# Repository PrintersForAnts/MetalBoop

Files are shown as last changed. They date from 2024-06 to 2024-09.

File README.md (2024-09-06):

# MetalBoop

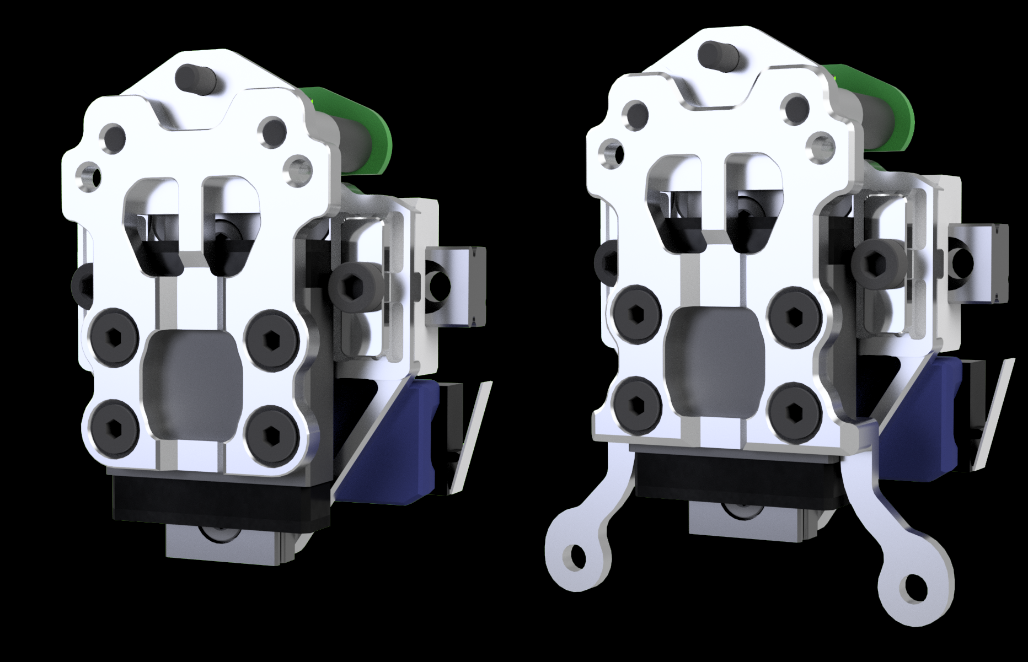
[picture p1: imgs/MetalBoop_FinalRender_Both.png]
MetalBoopRender
 

**Note: MetalBoop has been released as beta RC2 - second beta version on 6th of August 2024. Several bugs were fixed compared to RC1, but if you have no issues with RC1, there is no reason to upgrade. MetalBoop is an open source project - CAD files are available for the public [here](./CAD).**

---

### Index
1. [Introduction](#1-introduction)
2. [Features](#2-features)
3. [Compatibility](#3-compatibility)
4. [BOM](#4-bom)
5. [Assembly](#5-assembly)
6. [FAQ](#6-faq)
7. [Beta issues/changelog](#7-beta-issueschangelog)
8. [Contact](#8-contact)
9. [Credits](#9-credits)

---

## 1. Introduction

  A smaller metal version of plastic [Boop](https://github.com/PrintersForAnts/Boop).

  MetalBoop shares many of the same features as [Boop](https://github.com/PrintersForAnts/Boop) and [Tap](https://github.com/VoronDesign/Voron-Tap/) such as:
  * Microstep level accuracy.
  * Durability due to optical switch.
  * Simplicity - no dock and undock macros to fiddle with.
  * Zero probe distance.
  * Max chamber temperature: 100 C (when using OPB666N).

> [!NOTE]
> Input shaper improvement charts from beta testers are available [here](./results).

## 2. Features
- Higher rigidity due to use of metals instead of plastic.
- Plastic Boop reduces Y travel by ~ 14mm, MetalBoop by **only** 8mm.
- Using a wide MGW7 rail instead of MGN9 - rigidity is on par with MGN12C while taking 1mm less space in Y direction.
- Placement of a singular high temprature magnet eliminates the need to assemble and configure lateral magnets on both sides.
- Special optional front plate has two extra bottom mounting holes for better attachment of DragonBurner v8 toolhead.
- Tested with DragonBurner v8 to ensure as much space as possible for hotend wiring.
- Modified version of Vitaliis CNC Tap belt attachments.
- MetalBoop is shorter 10mm vertically - build plate crash is impossible.
- Simplified assembly using printed mounting jigs for MGW7 rail and magnet.

> [!WARNING]
> Unfortunately, MetalBoop does not bring only improvements. Due to increased rigidity between parts (magnet coupling), there is substantially more force needed to decouple Front plate. This means that nozzle presses against bed with much higher force and consequently can damage certain weak printpad surfaces. When deciding whether to use MetalBoop, you should consider this important fact.

## 3. Compatibility

Same as plastic [Boop](https://github.com/PrintersForAnts/Boop). Any Voron0 type toolhead compatible with front plate (eg. Mini StealthBurner). 100% compatible with [Dragon Burner v8 - DBv8](https://github.com/chirpy2605/voron/tree/main/V0/Dragon_Burner). All Hotends and all Extruders are supported.

## 4. BOM

| Part | Quantity | Links | Note
|---|---|---|---|
| CNC parts (2-part version) | 1 | [Open source CNC](./CAD/CNC) or [PCBWay](https://www.pcbway.com/project/shareproject/MetalBoop_2p_beta_RC1_de9ac2f4.html) | Order this if **you are NOT** using Dragon Burner V8 but any other Voron0 compatible toolhead such as Mini StealthBurner. You need to order two parts - Base plate and Front plate!
| CNC parts (2-part version for DBv8) | 1 | [Open source CNC](./CAD/CNC) or [PCBWay](https://www.pcbway.com/project/shareproject/Metal_Boop_DBv8_2p_beta_RC1_88e154ac.html) | Order this if **you are** using Dragon Burner V8. You need to order two parts - Base plate and Front plate!
| Linear rail MGW7C/STW7C 40mm | 1 | [Aliexpress](https://www.aliexpress.com/item/1005001499370117.html) <br>(EU) [Replimat](https://www.replimat.eu/mgw7c-40mm-medium-preload-rail-carriage/rt10182) | Z2 (medium) preload, 5mm edge-to-hole
| Magnet B842SH  | 1 | (NA) [Kj Magnetics](https://www.kjmagnetics.com/proddetail.asp?prod=B842SH) <br>(EU) [Replimat](https://www.replimat.eu/metalboop-magnet-b842sh/rt10176) | To secure magnet, RTV Silicone is needed. Make sure you have it or get high quality one.
| M3 10mm spacer  | 2 | [Aliexpress](https://www.aliexpress.com/item/1005003018651855.html) | Only needed if using 3-part version of MetalBoop
| M3 10mm standoff  | 2 | [Aliexpress](https://www.aliexpress.com/item/1005005462128073.html) | Only needed if using 2-part version of MetalBoop (can also use plastic standoffs)
| 2x Makerbeam T-slot nut - (drilled out to 3mm) | 2 | [Aliexpress](https://www.aliexpress.com/item/1005004891815148.html) | Optional - only used to additionally secure belts
| BHCS/SHCS M3x5 | 2 |  | Optional - only used to additionally secure belts
| BHCS/SHCS M3x22 | 2 |  | Only needed if using 3-part version of MetalBoop
| BHCS M3x6 | 2 |  | Only needed if using 2-part version of MetalBoop
| FHCS M3x5 | 8 |  | Make sure these are 5mm; 6mm version is too long!
| SHCS M3x4 | 1 |  | Used to mount top part of MGW7 rail
| SHCS M3x5 | 1/3/5 |  | Used to mount bottom part of MGW7 rail; get extra 2pcs if not using sensorless homing; get extra 2pcs if using DragonBurner V8
| Slim version of OptoTAP PCB (5V only) | 1 | (EU) [Replimat](https://www.replimat.eu/optotap-v1.3-opb666n/rt10181)<br> (EU) [Lab4450](https://lab4450.com/product/voron-tap-probe/) (select OptoTap v1.3 5v with Omron SX-EE398)<br>(NA) [Fabreeko](https://www.fabreeko.com/products/voron-tap-pcb?_pos=1&amp;amp;amp;amp;amp;amp;_psq=Tap&amp;amp;amp;amp;amp;amp;_ss=e&amp;amp;amp;amp;amp;amp;_v=1.0&amp;amp;amp;amp;amp;amp;variant=44462578368767) (select Voron TAP 5v) | Although either PCB type can be mounted, the larger version of the OptoTap PCB may interfere with either the extruder or extruder stepper.

> [!IMPORTANT]
> Current latest available version is beta RC2. Although, considerable amount of users are using MetalBoop already, MetalBoop is still in beta phase thus purchase, assemble and use at your own risk!

## 5. Assembly

> [!NOTE]
> Please, [contact us](#8-contact) if assembly manuals are unclear, so we can improve them. Thank you!

> [!TIP]
> You can always check out [CAD design file](./CAD) to see how parts fit together.

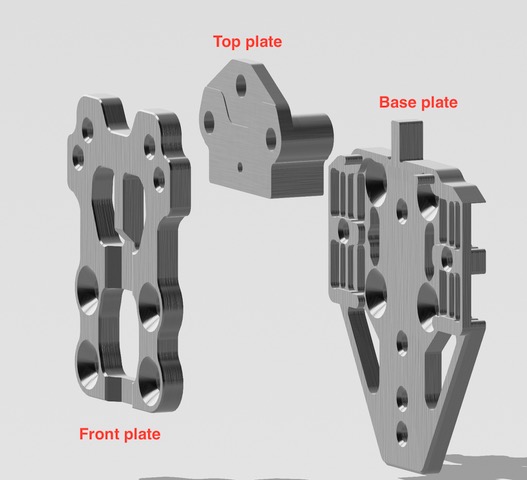
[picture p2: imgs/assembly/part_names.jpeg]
MetalBoopNames
   

#### A) Magnet

Start by assembling magnet because after this task you will have to wait 24 hours for RTV to cure. [Recommended to use printed jig to help with correct assembly.](https://github.com/PrintersForAnts/MetalBoop/tree/main/STL/jigs#assembly-of-magnet)

#### B) Belts

Next attach base plate to X rail cart together with belts as shown in the picture provided by Vitalii (**Vitalii's belt mount**). Make sure that both belts are of equal lengths!

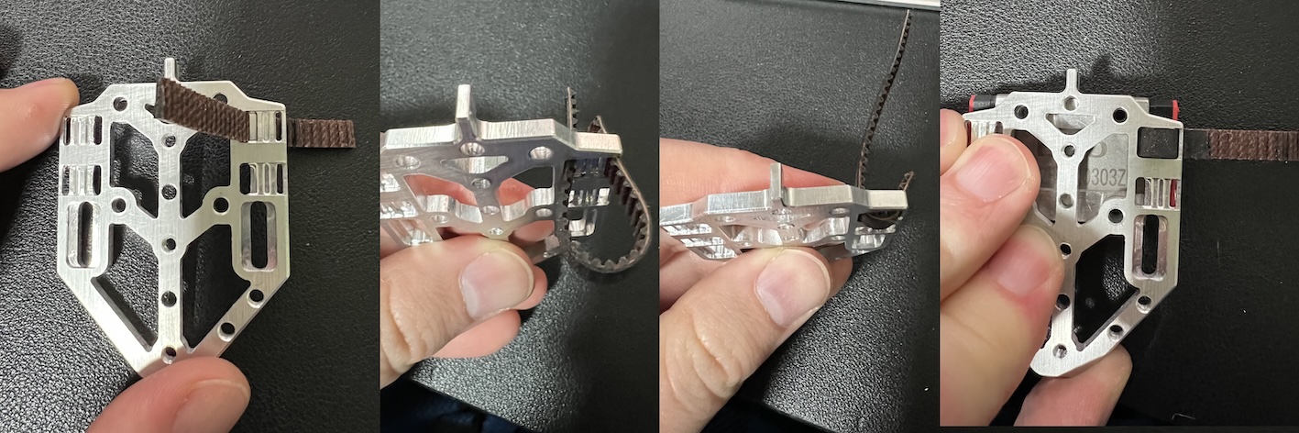
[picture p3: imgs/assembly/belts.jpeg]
MetalBoopBelts
 

Note that MetalBoop has additional M3 holes for securing belt the same way as plastic Boop. According to our tests, when Base plate is made out of Alu7075 or better, it is enough to secure belts using only Vitalii's belt mount. If you are not sure, you may additionally secure belts using Makerbeam T-slot nuts, but make sure you drill them out with 3mm drill bit before as holes in T-slot nuts must be without threads!

Base plate is secured to X rail cart using **4x FHCS M3x5mm**. You have to do this step before mounting MGW7 rail, otherwise you won't be able to reach these four screws.

#### C) MGW7 rail

Slide MGW7C cart off the linear rail onto plastic jig that was supplied with the rail and save it. You do not have to clean/grease this rail.
[Detailed instructions regarding assembly of MGW7 are here.](https://github.com/PrintersForAnts/MetalBoop/tree/main/STL/jigs#assembly-of-mgw7-rail)

#### D) Sensor

How to mount optotap sensor PCB depends whether you have 2-part or 3-part MetalBoop. 

> [!IMPORTANT]
> If using OPB666N sensor, you may have to extend standoffs/spacers by 0.5mm - 1.0mm because OPB666N is a bit larger and would not fit otherwise. You can do this by adding shims/washers in between standoffs/spacers and OptoTap PCB.

#### 2-part MetalBoop

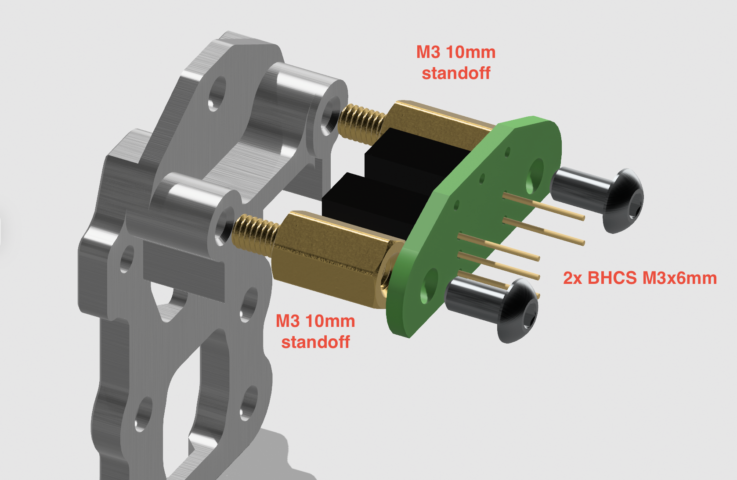
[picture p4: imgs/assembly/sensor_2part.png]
MetalBoopSensor2Part
 

#### 3-part MetalBoop

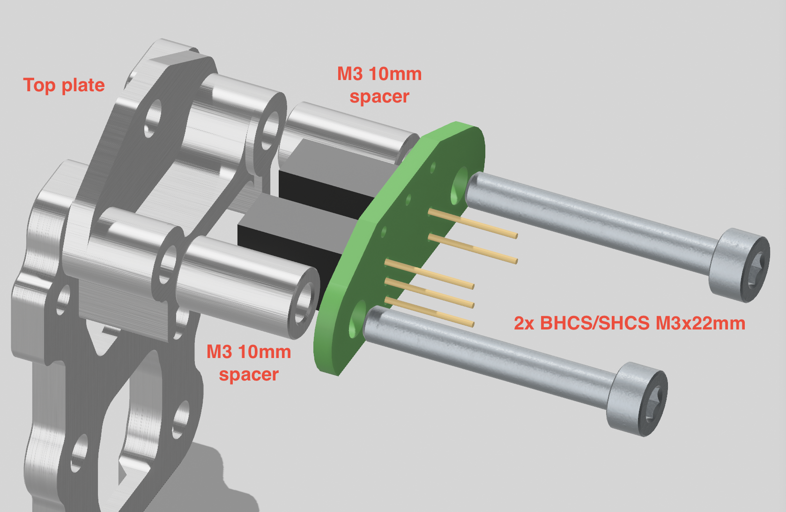
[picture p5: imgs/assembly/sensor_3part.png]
MetalBoopSensor3Part


#### E) Finish

Slide MGW7C cart back onto MGW7 rail from below and make sure that the cart doesn't slide off before you complete next step. Carefully bring assembled Front plate near assembled Base plate. When Front plate is very close to the Base plate, magnet's force will position Front plate. Adjust position of MGW7C cart so that 4 mounting holes on cart align with 4 holes on Front plate. Use **4x FHCS M3x5mm** screws to attach Front plate to the cart. 

It is recommended to test MetalBoop before you continue with mounting toolhead. If boop'ing doesn't work correctly, then the issue is most likely in vertical position of sensor. You can adjust that by moving MGW7 rail slightly down and retightening its mounting screws ([make sure to use jigs - clamps](https://github.com/PrintersForAnts/MetalBoop/tree/main/STL/jigs#assembly-of-mgw7-rail)).

#### F) Misc

[If you are not using sensorless homing but rather endstop switches, please check out this page.](https://github.com/PrintersForAnts/MetalBoop/tree/main/STL#xy-homing-using-endstops)

## 6. FAQ

1. <ins>When is it going to be available?</ins>
  * Second public beta RC2 version has just been released. Note that this is public beta and there may be some small issues here and there. We are doing our best to list all found issues [here](#7-beta-issueschangelog). If you find any issue, error with CAD design or error in GitHub page, please [contact us and report it](#8-contact).
        
2. <ins>What else besides the BOM do I need?</ins>
  * Unfortunately, from the start, we expect that for the first few weeks or months, you will also have to get parts manufactured on your own. CNC design files are available [here](./CAD/CNC). There are online services such as [JLCPCB](https://jlcpcb.com/) or [PCBWAY](https://www.pcbway.com/) which can make the parts. After some time, we hope vendors will pick up the design and make kits with already manufactured metal parts so you won’t have to do anything but purchase a kit and assemble it.

3. <ins>What is the difference between 2-part and 3-part MetalBoop?</ins>
  * Boop usually consists of 3 main metal parts; those are:
    * Base plate (screws into X rail cart and to which belts are attached),
    * Front plate (screws into Boop's vertical MGW7 rail and toolhead) and
    * Top plate (screws into Front plate and where optical sensor PCB attaches to).
      
    MetalBoopNames
    
This configuration is called 3-part MetalBoop and is cheaper for CNC production. 2-part MetalBoop is optimisation to further increase rigidity by merging Front and Top plates together. But while more efficient and also easier to assemble, it can be 5-20 $ more expensive to produce. Both versions are available and the choice which one to get and assemble is yours.

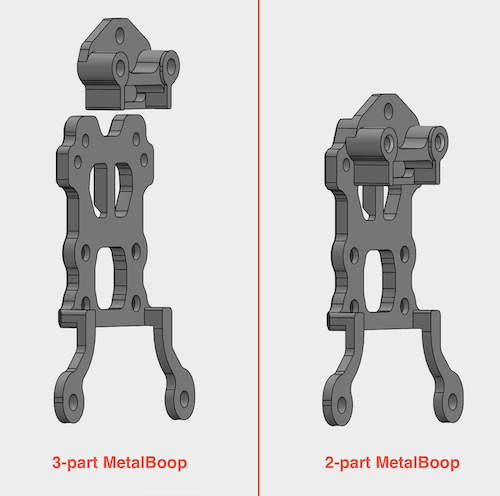
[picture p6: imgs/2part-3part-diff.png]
MetalBoopDifference
   

4. <ins>How much downforce is there?</ins>
  * While for Voron Tap is being said that it needs 600g of force to uncouple, we measured MetalBoop needs around 1500g! This means that it is way more rigidly coupled than Tap, which should improve your input shaper charts and allows you to print with higher accelerations while maintaining same level of print quality. Note that more downforce is not always better - higher force can damage your printpad, so be aware of that when choosing MetalBoop. We recommend using textured PEI plate, invar plate or any other plate that has strong surface.

5. <ins>Is it mandatory to use T-nuts and M3 screws to attach belts?</ins>
  * While for plastic Boop, simply hooking belts between rail and plastic part turned out not to be enough, when using aluminum parts, this is not the case. Using additional T-nuts and screws is therefore completely optional thus redundant. 
        
6. <ins>I would like to sell manufactured metal parts and/or kits. Can I do that free of charge or do I have to ask your permission or pay for license, royalties, etc?</ins>
  * MetalBoop is completely open source, released under GPLv3 license. You can freely use designs for your commercial purposes free of charge.

7. <ins>I am stuck with assembly/I do not understand assembly process. What should I do?</ins>
  * Get in [contact with us](#8-contact) and ask for help. While also providing help to you, we will do our best to also update currently developed manuals on Github under [Assembly topic](#5-assembly).

## 7. Beta issues/changelog
> [!NOTE]
> Marked issues will be fixed in the following version.

_Currently no known/reported issues in latest version._

### Beta RC2 fixes:
- [x] https://github.com/PrintersForAnts/MetalBoop/issues/1 Dragon hotend: small part of silicone sock needs to be cut for MetalBoop to fully fit.

## 8. Contact
You can get in contact with us by:
- Submitting [GitHub issue](https://github.com/PrintersForAnts/MetalBoop/issues) or
- [Discord #CNC_boop channel](https://discord.com/channels/825469421346226226/1222971771444006996).

## 9. Credits
- [Kizime123](https://github.com/Kizime123) for CAD design and
- [djeZo888](https://github.com/djeZo888) for sponsoring, GitHub page and initial testings.

Credits also go to:
- [Voron TAP](https://github.com/VoronDesign/Voron-Tap/) designers,
- [Boop](https://github.com/PrintersForAnts/Boop) designers,
- [AndyABG](https://github.com/AndyABG),
- [Vitalii](https://github.com/Vitalii3D-xyz),
- Solders.

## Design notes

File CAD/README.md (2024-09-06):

Currently available public beta RC2 version (STEP): [Metal_Boop_beta_RC2.step](./Metal_Boop_beta_RC2.step)

CNC design files are available [here](./CNC).

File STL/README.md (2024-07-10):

> [!TIP]
> Parts in this folder should be printed prior starting with assembly of MetalBoop.

---

### Assembly helper parts - jigs

[More information is available here.](https://github.com/PrintersForAnts/MetalBoop/tree/main/STL/jigs)

---

### Sensorless XY Homing

No additional assembly is required.

---

### XY Homing using endstops

[**endstop_holder_x1.stl**](./endstop_holder_x1.stl) is plastic part that you have to print and attach to the back side of the Base plate when you are not using sensorless homing. Print it with material that can sustain chamber temperatures you'll use when printing, eg. same material as for other printer parts that are inside chamber (such as ABS, ASA,...). Use Voron recommended slicer settings.

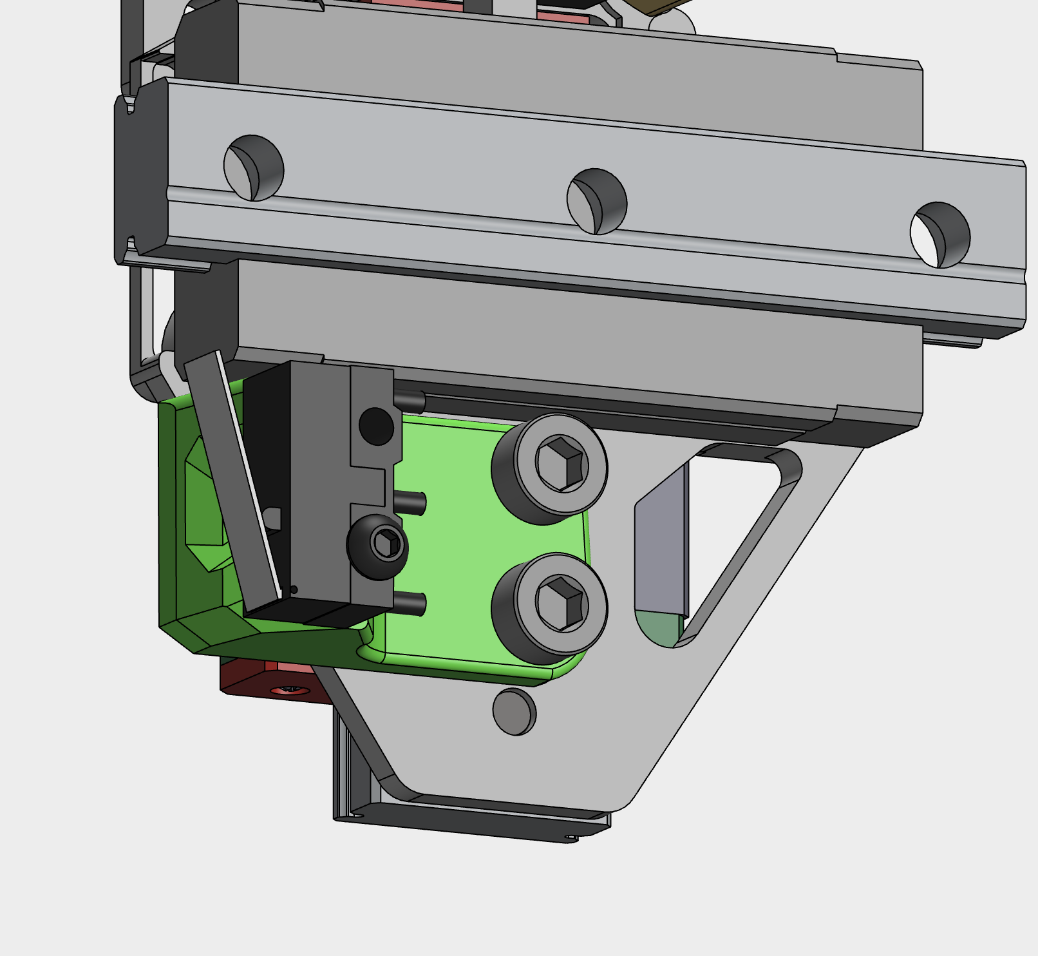
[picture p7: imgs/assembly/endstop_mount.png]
Endstop-Mount


Plastic part is attached to the Base plate using **two SHCS M3x5mm screws** (**do not use longer than 5mm**, because there is not enough space!). Endstop switch is attached to the plastic part using **one M2x10mm self-tapping screw**.

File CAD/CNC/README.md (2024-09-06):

Use following files for CNC machining depending on which version (2-part, 3-part) or toolhead you use (Dragon Burner v8, any toolhead). Technical drawings are used to mark threaded holes.

> [!NOTE]
> It is strongly suggested to use following links that are for **beta RC2** files that you should use which include all known discovered and fixed bugs up to date.

### 2-part (any toolhead)
- [Base plate CNC CAD](./base/P0011_REV_E.step)
- [Base plate technical drawing](./base/P0011_REV_E.pdf)
- [Front plate CNC CAD](./2-part/stock/P0019_REV_B.step)
- [Front plate technical drawing](./2-part/stock/P0019_REV_B.pdf)

### 2-part (Dragon Burner v8)
- [Base plate CNC CAD](./base/P0011_REV_E.step)
- [Base plate technical drawing](./base/P0011_REV_E.pdf)
- [Front plate CNC CAD](./2-part/DB8/P0017_REV_C.step)
- [Front plate technical drawing](./2-part/DB8/P0017_REV_C.pdf)

### 3-part (any toolhead)
- [Base plate CNC CAD](./base/P0011_REV_E.step)
- [Base plate technical drawing](./base/P0011_REV_E.pdf)
- [Front plate CNC CAD](./3-part/stock/P0004_REV_G.step)
- [Front plate technical drawing](./3-part/stock/P0004_REV_G.pdf)
- [Top plate CNC CAD](./3-part/top/REV_C_TOP_PLATE.step) (no threaded holes, no tehnical drawing needed)

### 3-part (Dragon Burner v8)
- [Base plate CNC CAD](./base/P0011_REV_E.step)
- [Base plate technical drawing](./base/P0011_REV_E.pdf)
- [Front plate CNC CAD](./3-part/DB8/P0010_REV_E.step)
- [Front plate technical drawing](./3-part/DB8/P0010_REV_E.pdf)
- [Top plate CNC CAD](./3-part/top/REV_C_TOP_PLATE.step) (no threaded holes, no tehnical drawing needed)

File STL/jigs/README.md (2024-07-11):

> [!TIP]
> Parts in this folder should be printed prior starting with assembly of MetalBoop.

### Assembly of magnet

> [!TIP]
> **It is recommended to perform this assembly task first because 24 hours is needed for RTV to cure.**

[**jig_magnet_x1.stl**](./jig_magnet_x1.stl) is used to help you with installation of magnet into oval hole. It makes sure that magnet sits in the middle of the hole and is in fully horizontal position. Print this jig using PLA or PETG with high details (recommended 0.4mm nozzle, Voron recommended slicer settings but with 0.1mm layer height).

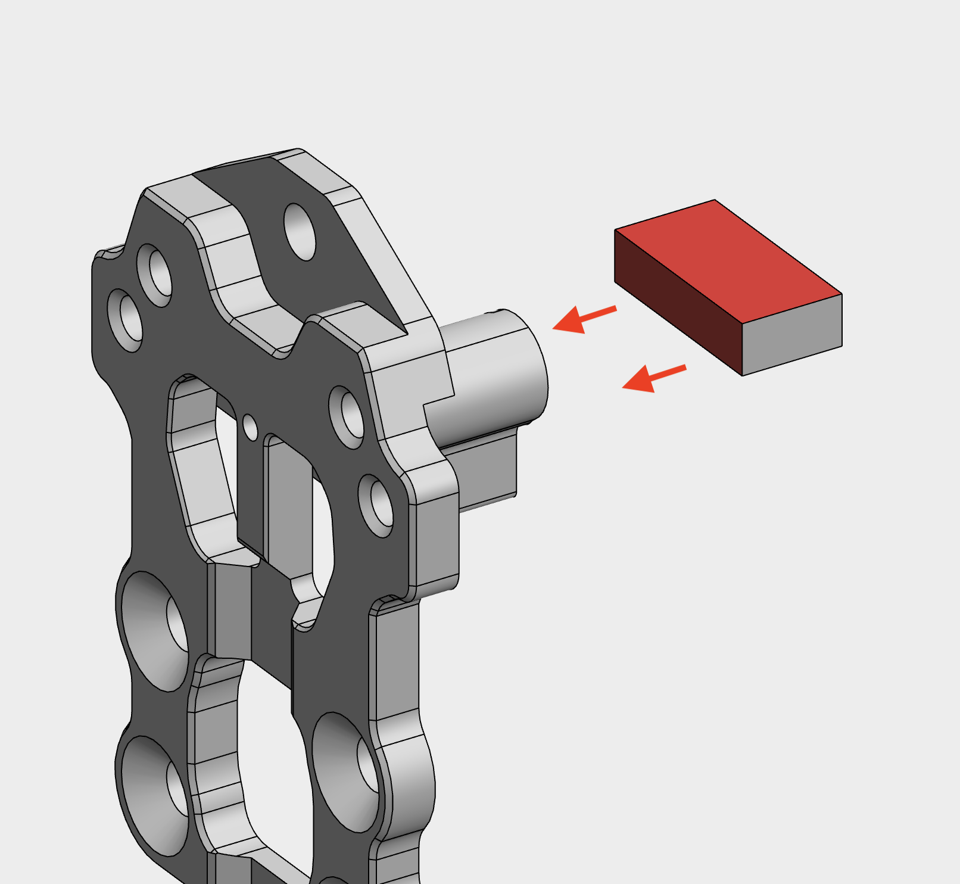
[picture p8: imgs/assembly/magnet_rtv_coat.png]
Magnet-RTV-Coat


Using flat surface tool such as credit card **evenly** coat two sides of magnet that touch insides of the hole with **thin** layer of RTV (check image above - two RTV coated sides are colored in red). Carefully insert magnet into the hole and try to position it in the middle. Then put the jig on the top and secure it with two M3 screws to nearby M3 holes (any short M3 screws are OK to be used). Leave this built assembly for 24 hours so RTV can cure.

> [!TIP]
> You can use hole in the middle of the jig and small hole in front aluminum part to poke magnet with non-magnetic stick to make sure it doesn't move around. If it does, then reprint jig scaled down for few 0.1% dimensions or properly tune your 3D printer.

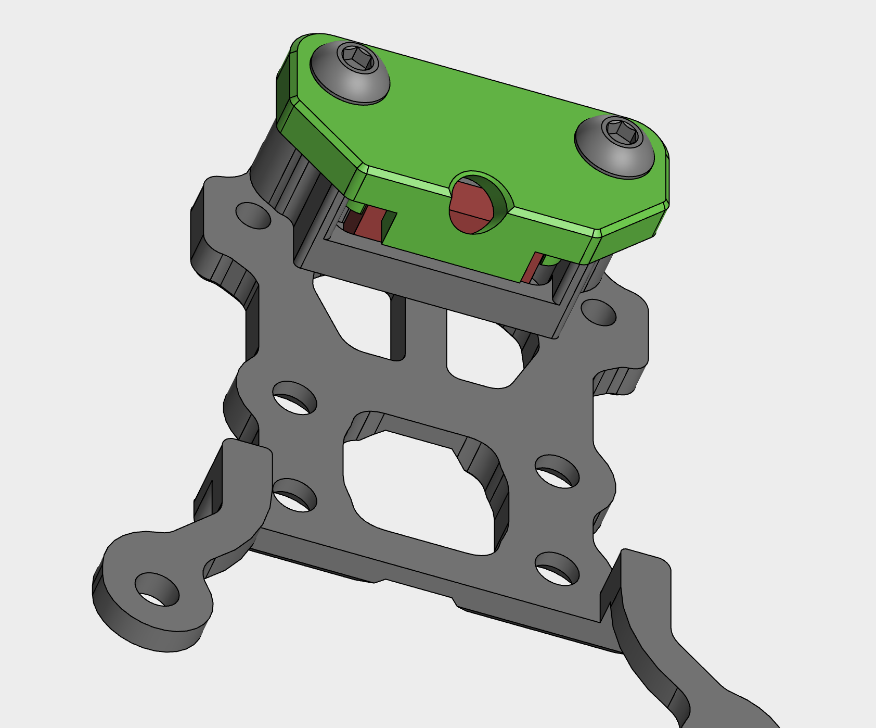
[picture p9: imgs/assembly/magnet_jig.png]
Magnet-Jig


After 24h unscrew M3 screws and remove the jig. Verify that the magnet is properly installed in the hole and cannot move (as in the picture below). If there is any RTV residue left on the bottom side of the magnet, you have to scrape that off, otherwise it will interfere with magnet's ability to touch top of the MGW7 rail with whole surface.

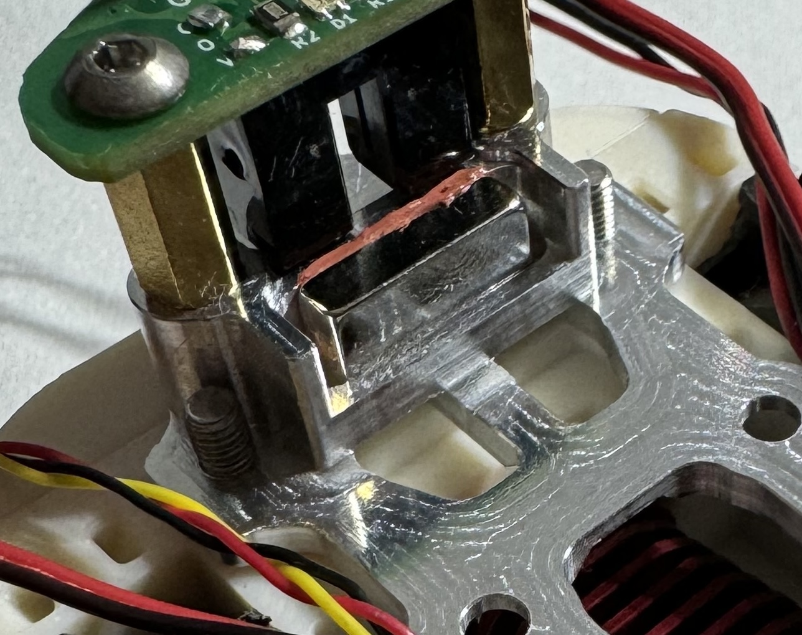
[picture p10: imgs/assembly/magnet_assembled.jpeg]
Magnet-Assembled


---

### Assembly of MGW7 linear rail

[**jig_rail_x2.stl**](./jig_rail_x2.stl) needs to be printed two times. These two parts are used to help secure MGW7 linear rail to the Base plate in fully vertical position - working as clamps. Print in PLA or PETG with at least Voron recommended slicer settings or better (more walls/infill). Clamps must be very rigid. If clamps are either too small to fit or too loose to fit firmly, scale them in slicer by few 0.1% up or down and reprint. Do that until you have clamps that fit firmly, but not too tight. You know that you have good clamps when rail doesn't move in any direction being clamped to the Base plate with only these two printed clamps (no screws).

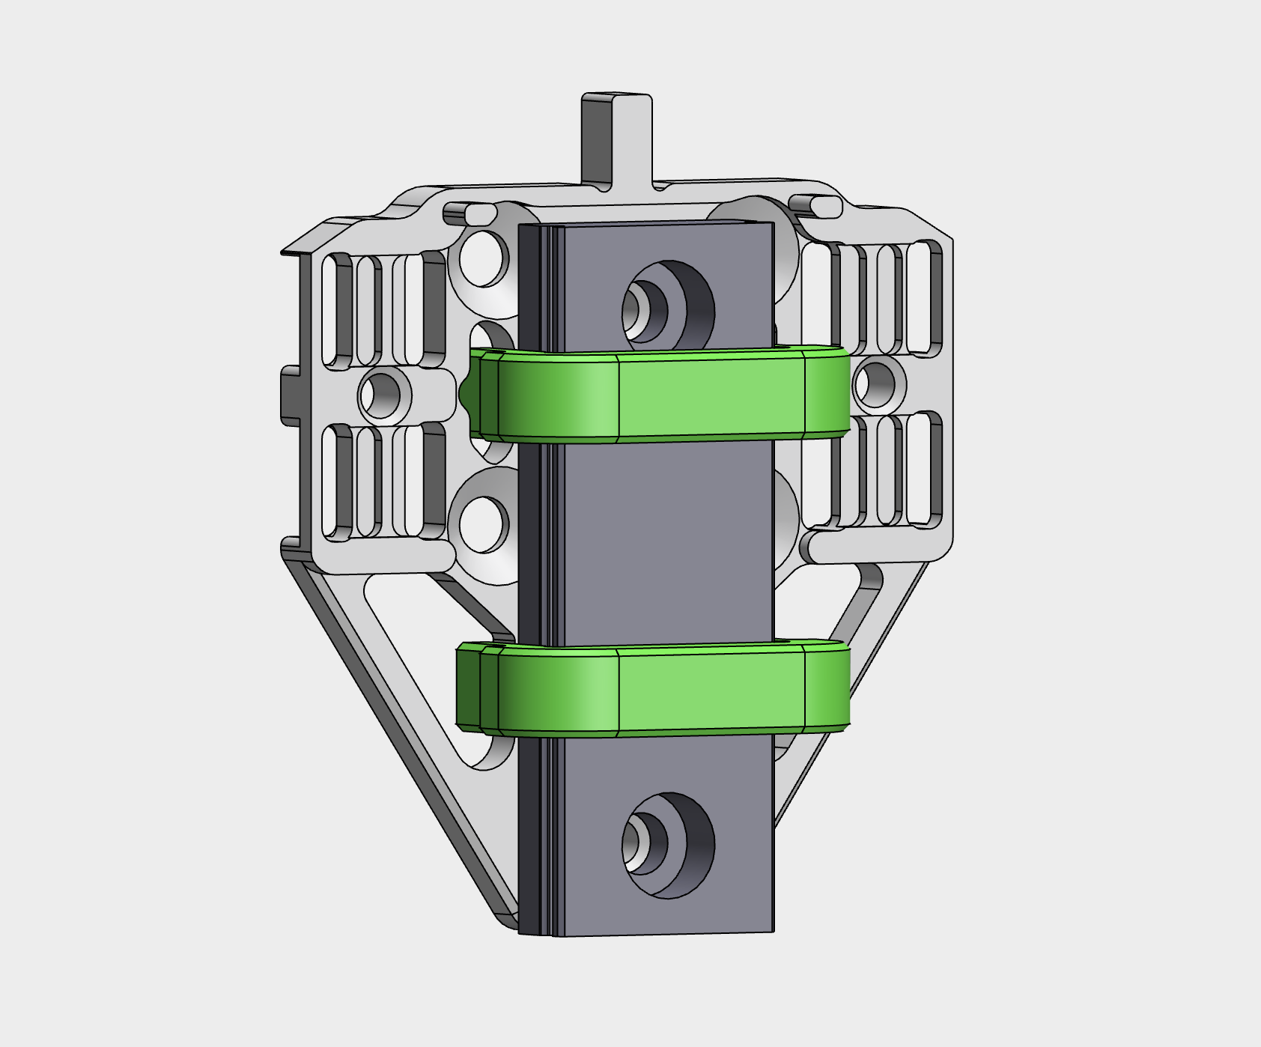
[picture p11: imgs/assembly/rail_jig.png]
Rail-Jig


Use two printed samples of this jig (clamps) when securing MGW7 rail to the Base plate. MGW7 linear rail must be in fully vertical position for MetalBoop to work properly. If it isn't when M3 screws that attach rail to the base plate are tightened, then loose these M3 screws and realign rail using printed clamps and tighten M3 screws again.

Use **SHCS M3x4mm** to secure upper part of the linear rail and **SHCS M3x5mm** to secure lower part of the linear rail. Shorter screw is used because there is X linear rail cart under base plate and 5mm long screw would not fit.

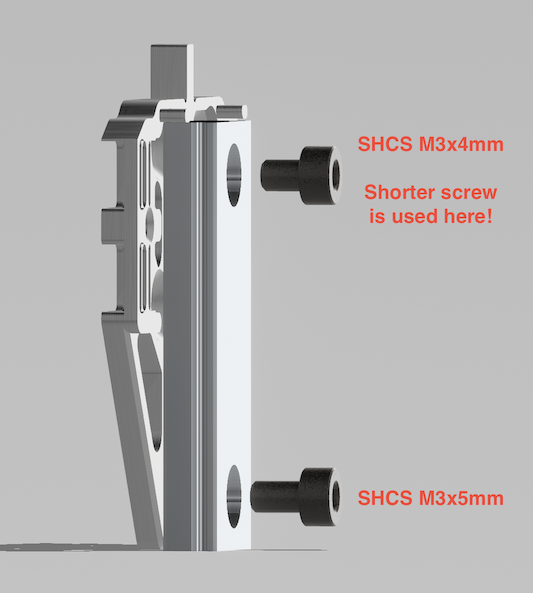
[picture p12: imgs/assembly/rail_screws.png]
Rail-Screws


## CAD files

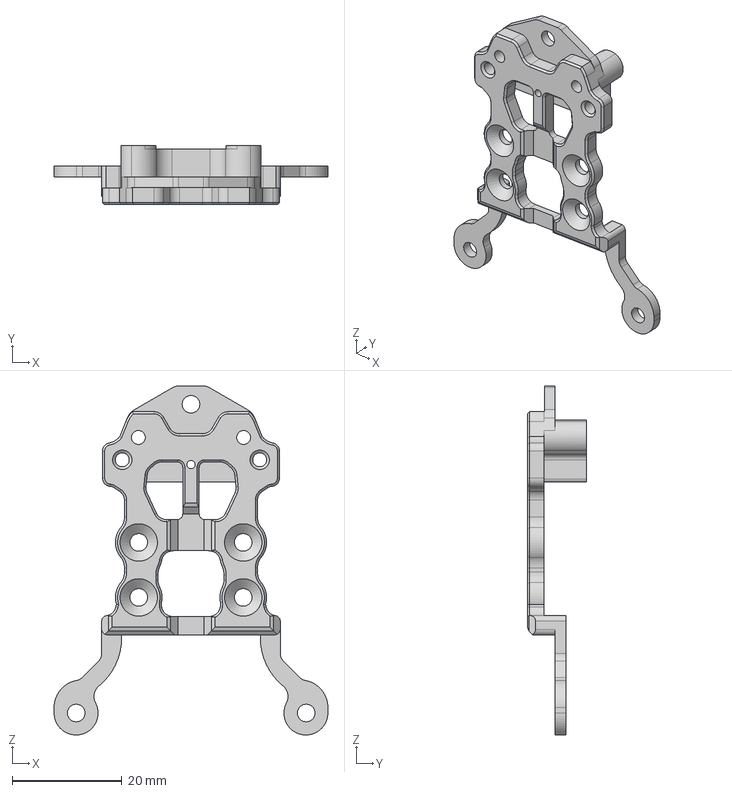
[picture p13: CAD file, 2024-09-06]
CAD/CNC/2-part/DB8/P0017_REV_C.step
49.8 x 10.8 x 63.5 mm

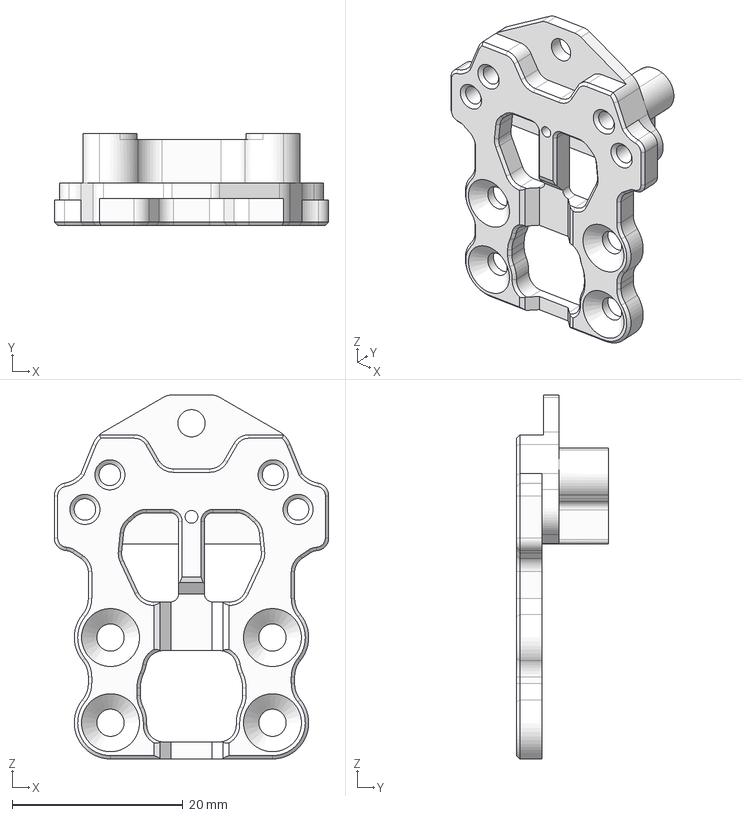
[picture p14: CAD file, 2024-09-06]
CAD/CNC/2-part/stock/P0019_REV_B.step
32.2 x 10.8 x 42.7 mm

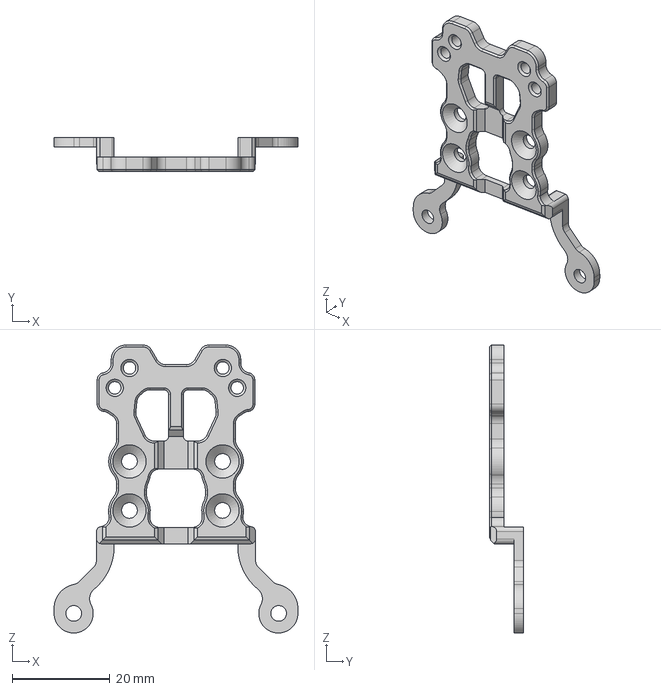
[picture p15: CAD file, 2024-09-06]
CAD/CNC/3-part/DB8/P0010_REV_E.step
49.8 x 7.01 x 58.8 mm

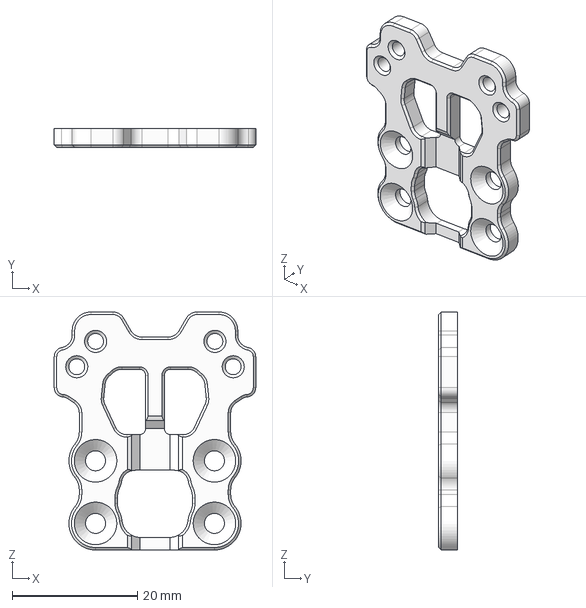
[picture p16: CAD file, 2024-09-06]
CAD/CNC/3-part/stock/P0004_REV_G.step
32.2 x 3.00 x 38.0 mm

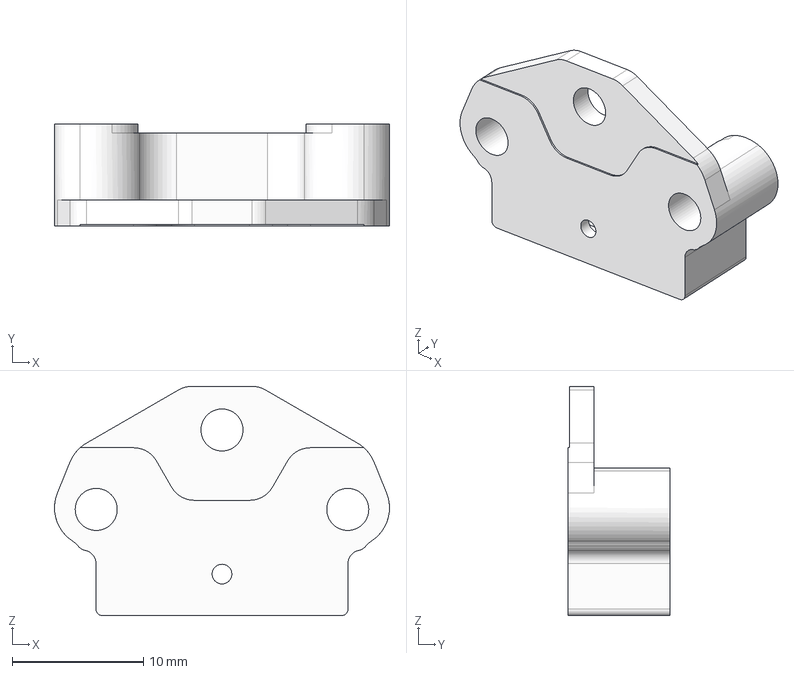
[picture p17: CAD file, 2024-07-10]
CAD/CNC/3-part/top/REV_C_TOP_PLATE.step
25.5 x 7.80 x 17.4 mm

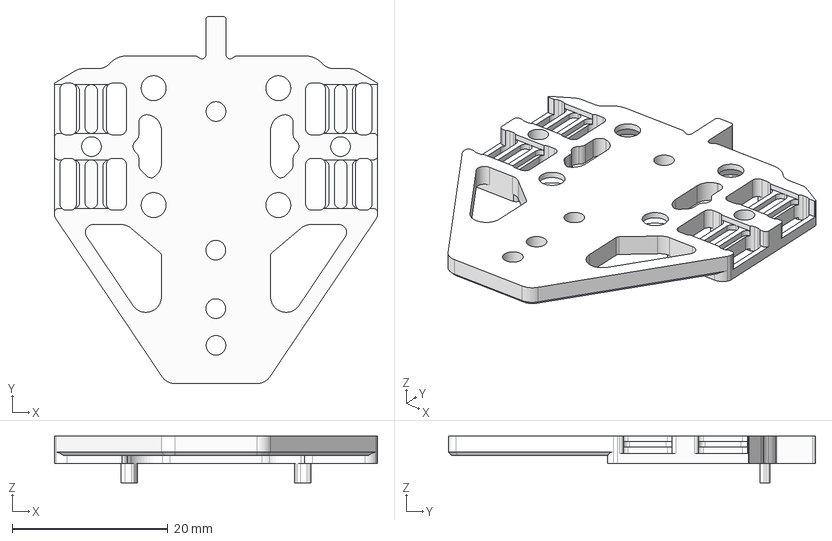
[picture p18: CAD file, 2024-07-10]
CAD/CNC/base/P0011_REV_E.step
41.4 x 47.1 x 6.00 mm

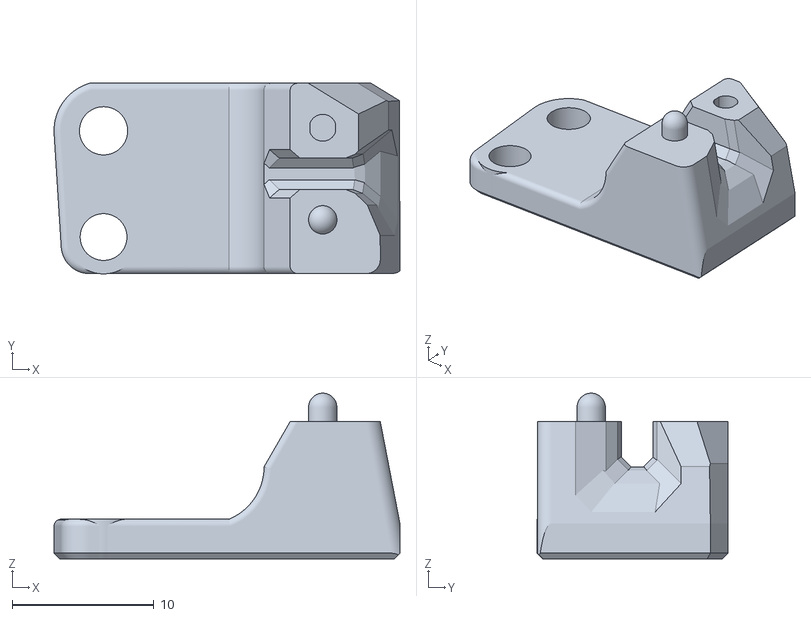
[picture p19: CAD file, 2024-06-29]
STL/endstop_holder_x1.stl
24.4 x 13.5 x 11.7

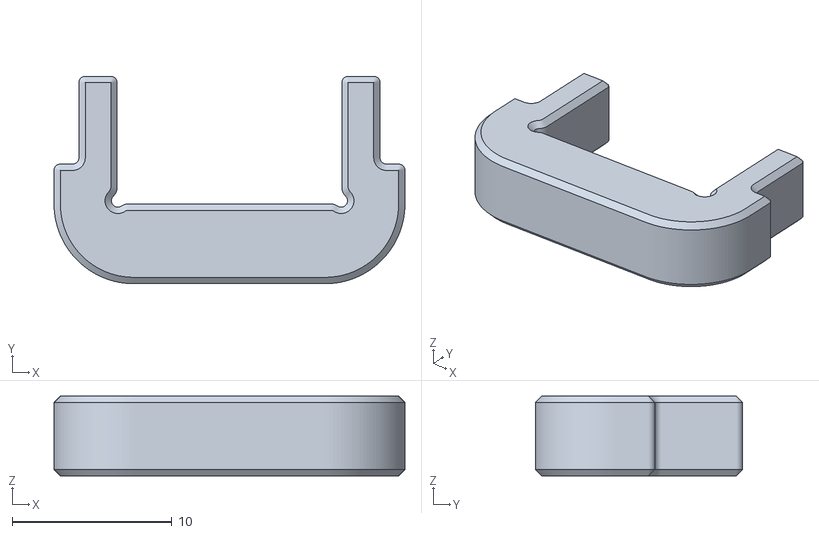
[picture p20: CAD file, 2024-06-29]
STL/jigs/jig_rail_x2.stl
22.0 x 13.0 x 5.00

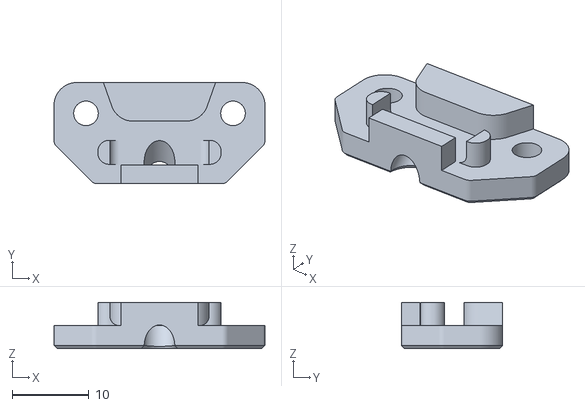
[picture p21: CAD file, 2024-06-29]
STL/jigs/jig_magnet_x1.stl
27.5 x 13.2 x 6.00

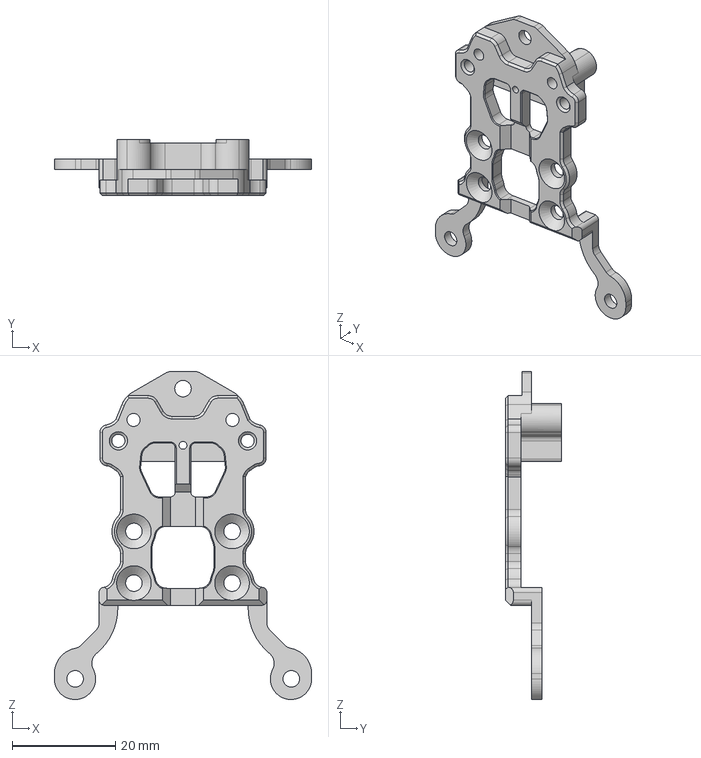
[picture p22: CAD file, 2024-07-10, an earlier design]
CAD/CNC/2-part/DB8/P0017_REV_B.step
49.8 x 10.8 x 63.5 mm

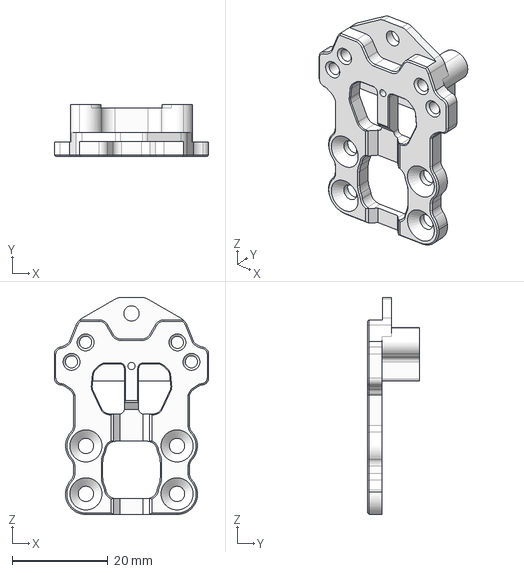
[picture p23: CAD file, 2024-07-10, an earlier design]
CAD/CNC/2-part/stock/P0019_REV_A.step
32.2 x 10.8 x 45.2 mm

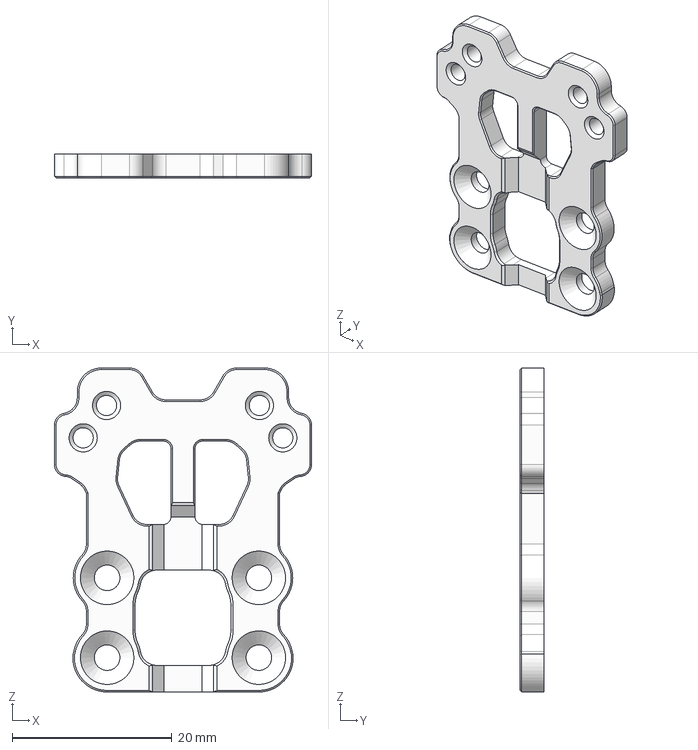
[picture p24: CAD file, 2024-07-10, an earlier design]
CAD/CNC/3-part/stock/P0004_REV_F.step
32.2 x 3.00 x 40.6 mm

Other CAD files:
CAD/CNC/3-part/DB8/P0010_REV_D.step

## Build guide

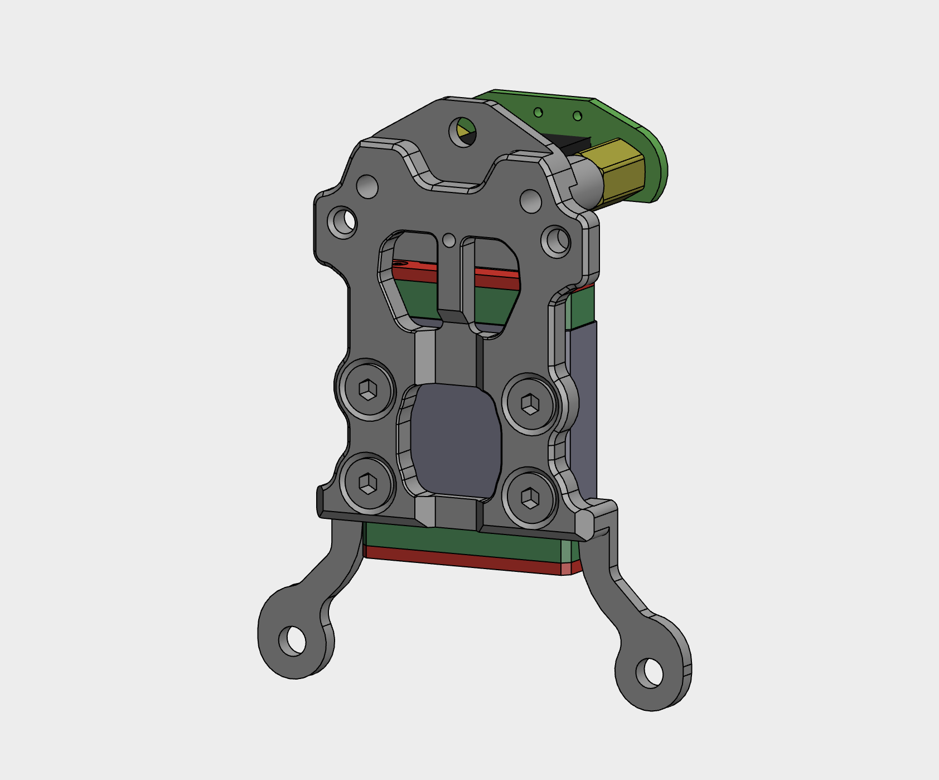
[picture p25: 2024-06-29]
imgs/assembly/front_plate_assembly_3.png

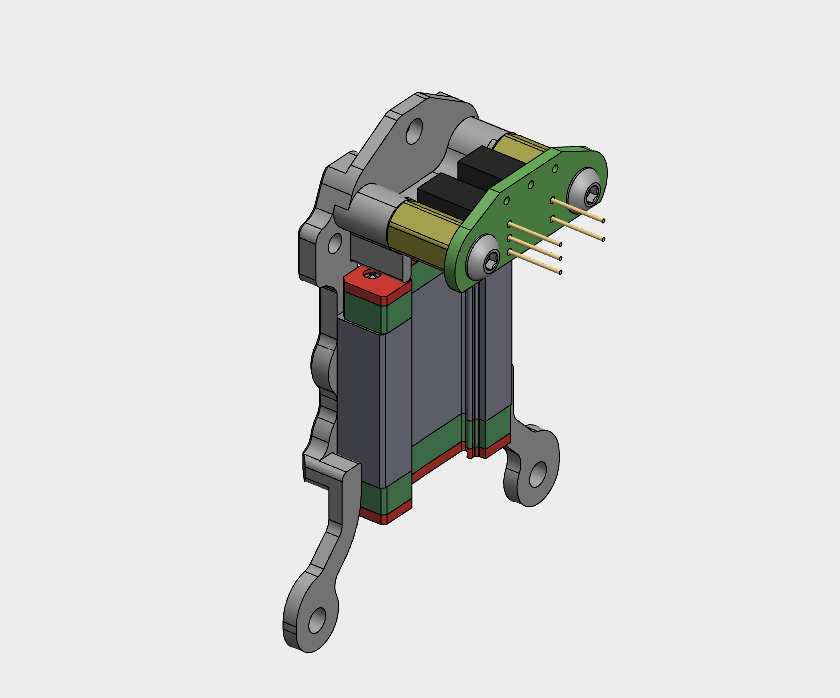
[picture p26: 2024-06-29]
imgs/assembly/front_plate_assembly_1.png

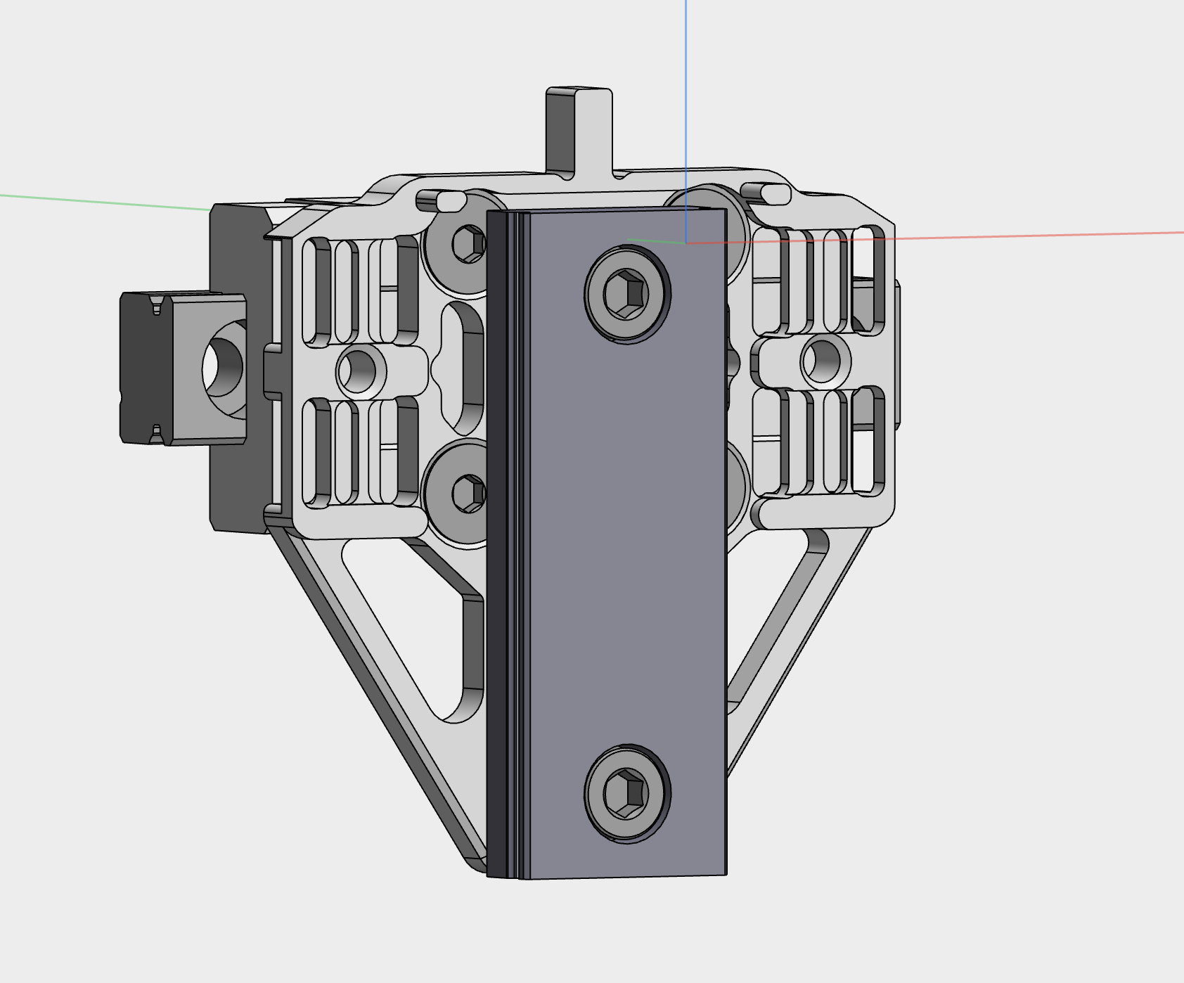
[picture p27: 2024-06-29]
imgs/assembly/base_plate_assembly.png

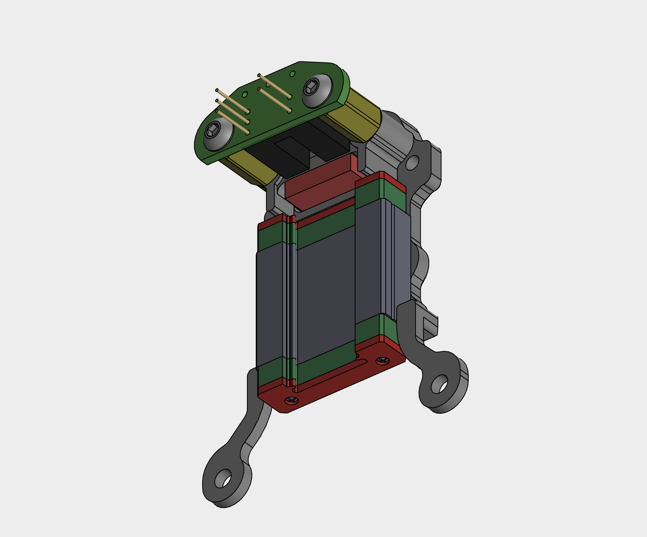
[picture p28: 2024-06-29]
imgs/assembly/front_plate_assembly_2.png

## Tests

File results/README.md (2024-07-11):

IS charts | Comment/review by beta tester
----------|---------
[betatester01](./betatester01) | `Metal Boop increased my speed a lot. Right now with Metal Boop I can push my printer speed a lot without losing quality. Also, I don't need to worry about cracked plastic Boop; I just install metal parts and I can stop worrying about heat softening plastic Boop parts. I really recommend Metal Boop to everyone.`
[betatester02](./betatester02) | 
[betatester03](./betatester03) | `its the lightest contact probe i had on all of my printers, it is easy to assemble and pretty light. its sturdy enough to get good results without compromises. only negativ think i can say is that it will pull cash out of your pocket for one time xD`

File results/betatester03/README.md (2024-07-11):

Axis | Plastic Boop | Vitalii's Boop | Metal Boop
-----|--------------|----------------|-----------
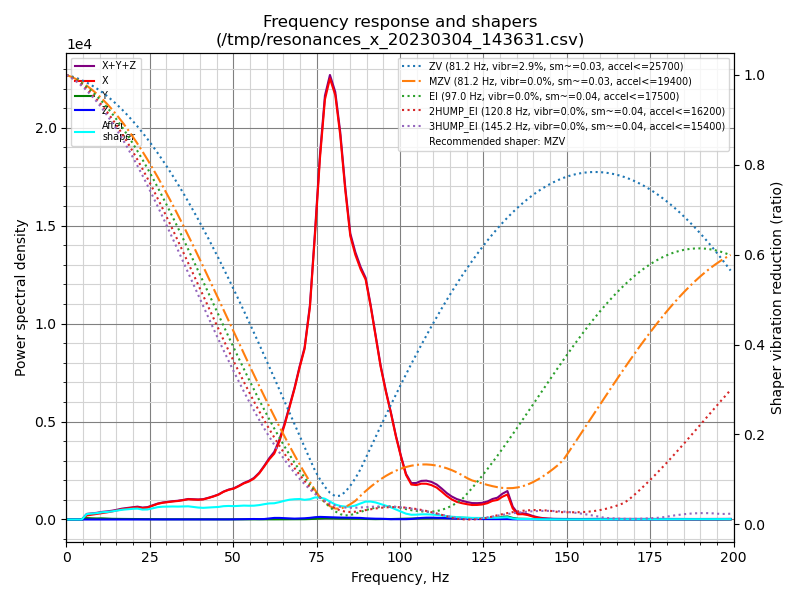
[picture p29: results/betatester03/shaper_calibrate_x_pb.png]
bt03-plastic-x
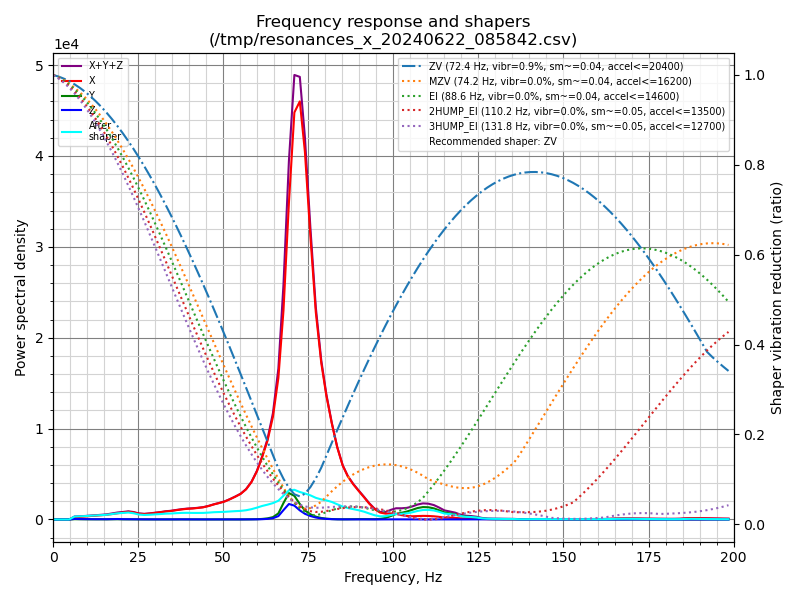
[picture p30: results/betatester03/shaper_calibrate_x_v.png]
bt03-vitaliis-x
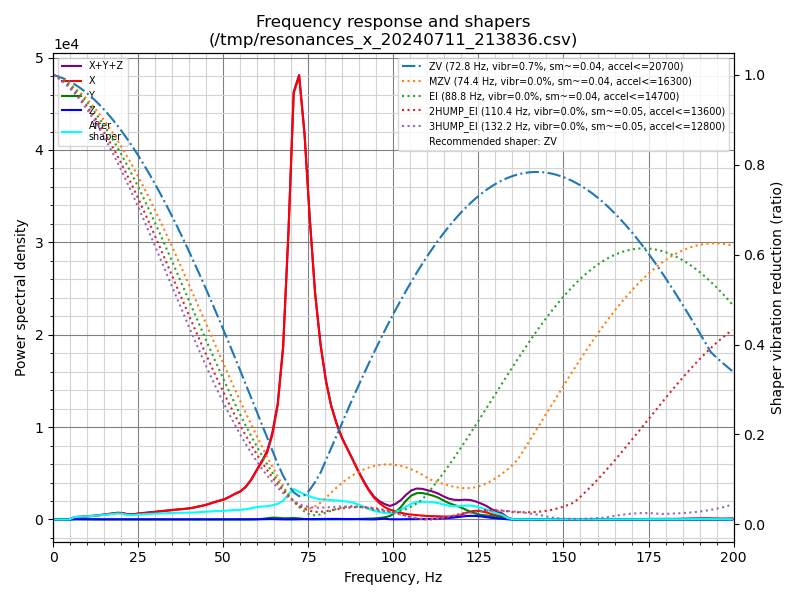
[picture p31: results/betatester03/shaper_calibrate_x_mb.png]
bt03-metal-x
X |  | | 
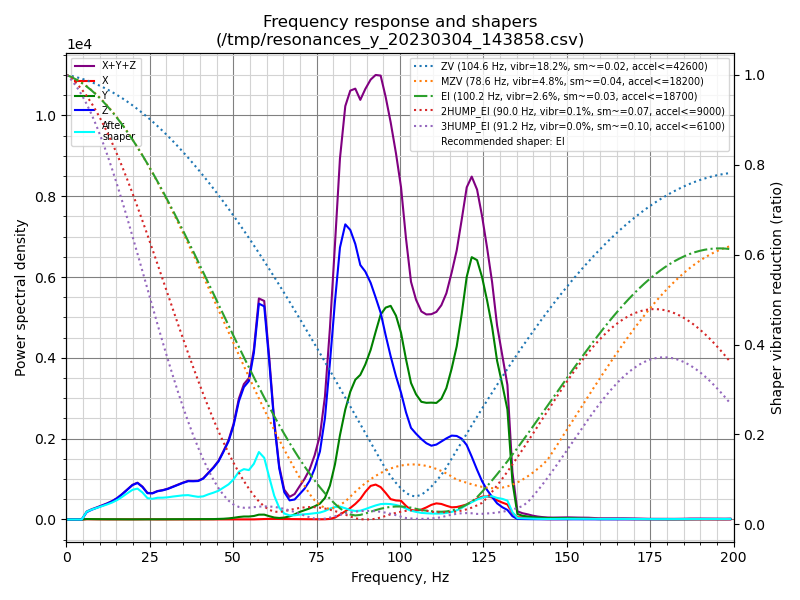
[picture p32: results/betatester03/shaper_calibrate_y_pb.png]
bt03-plastic-y
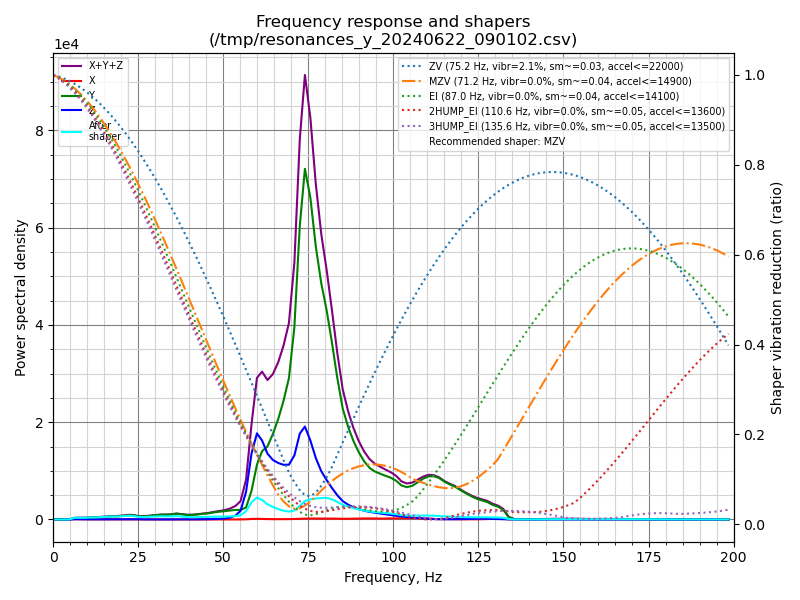
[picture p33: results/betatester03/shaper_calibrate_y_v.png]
bt03-vitaliis-y
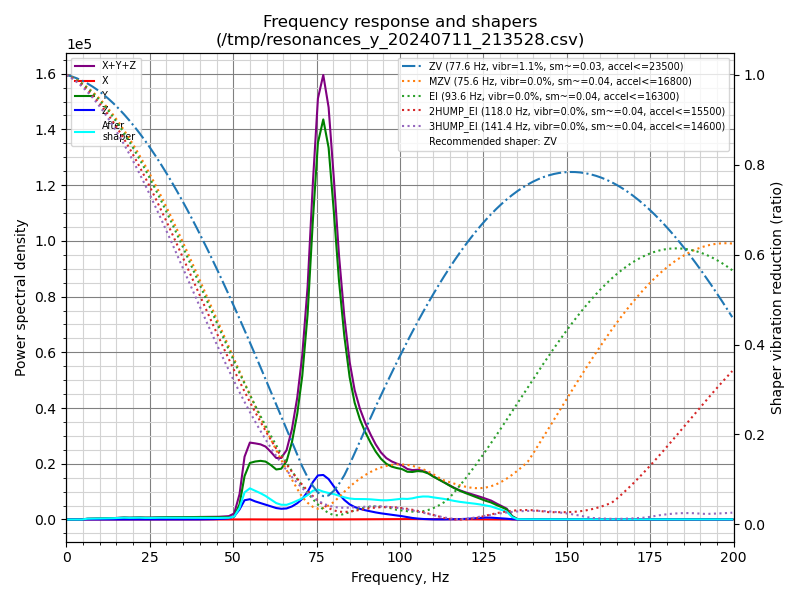
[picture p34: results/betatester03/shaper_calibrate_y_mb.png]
bt03-metal-y
Y |  | |

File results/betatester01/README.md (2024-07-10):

Axis | Plastic Boop | Metal Boop
-----|--------------|-----------
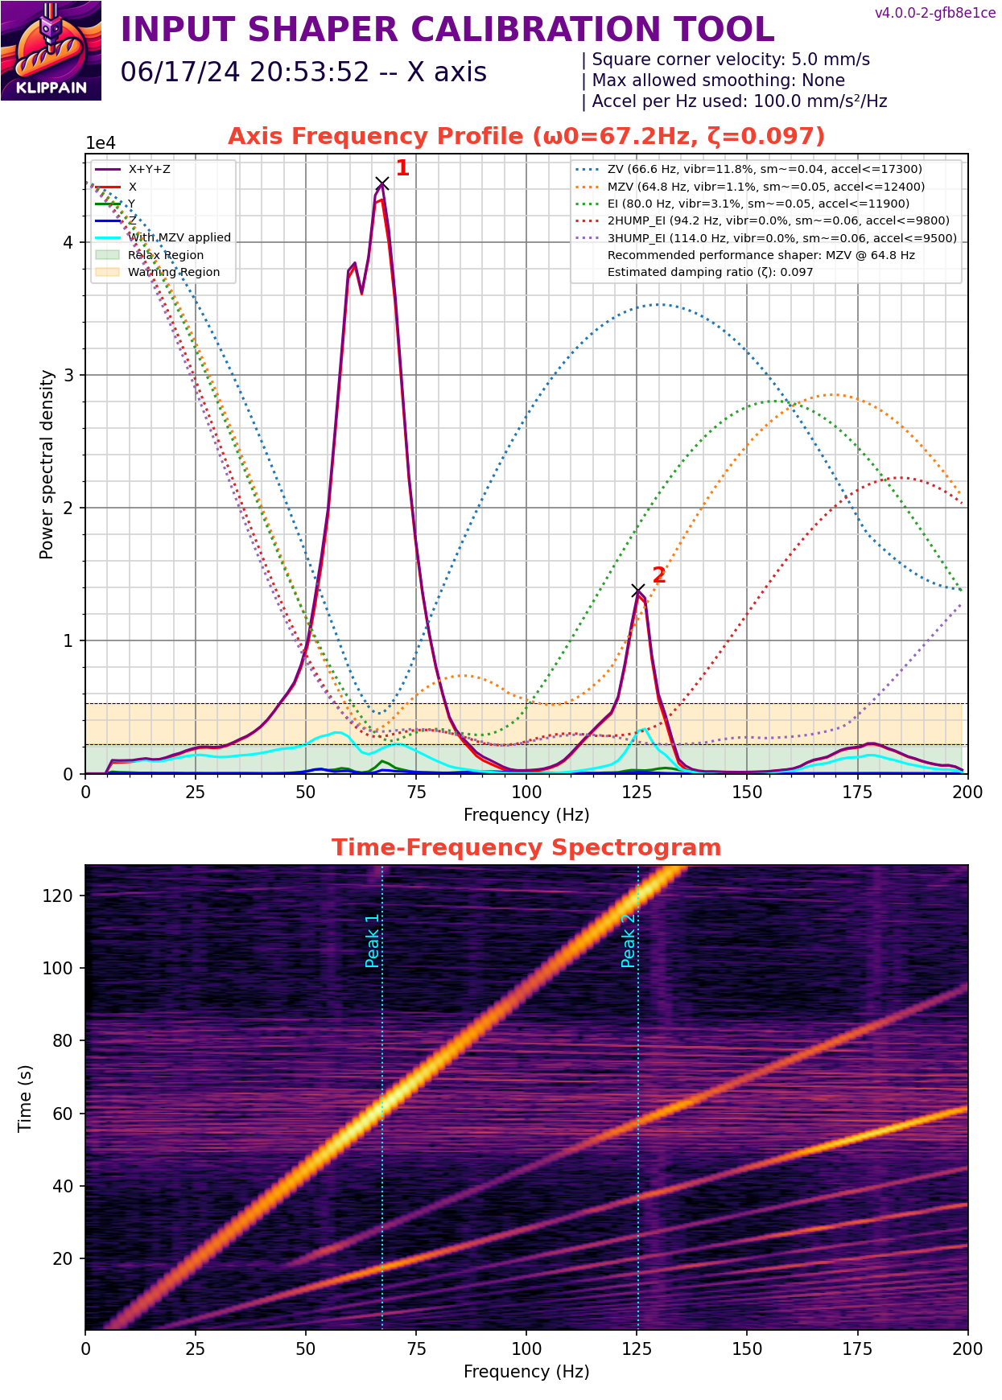
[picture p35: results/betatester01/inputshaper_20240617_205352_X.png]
bt01-plastic-x
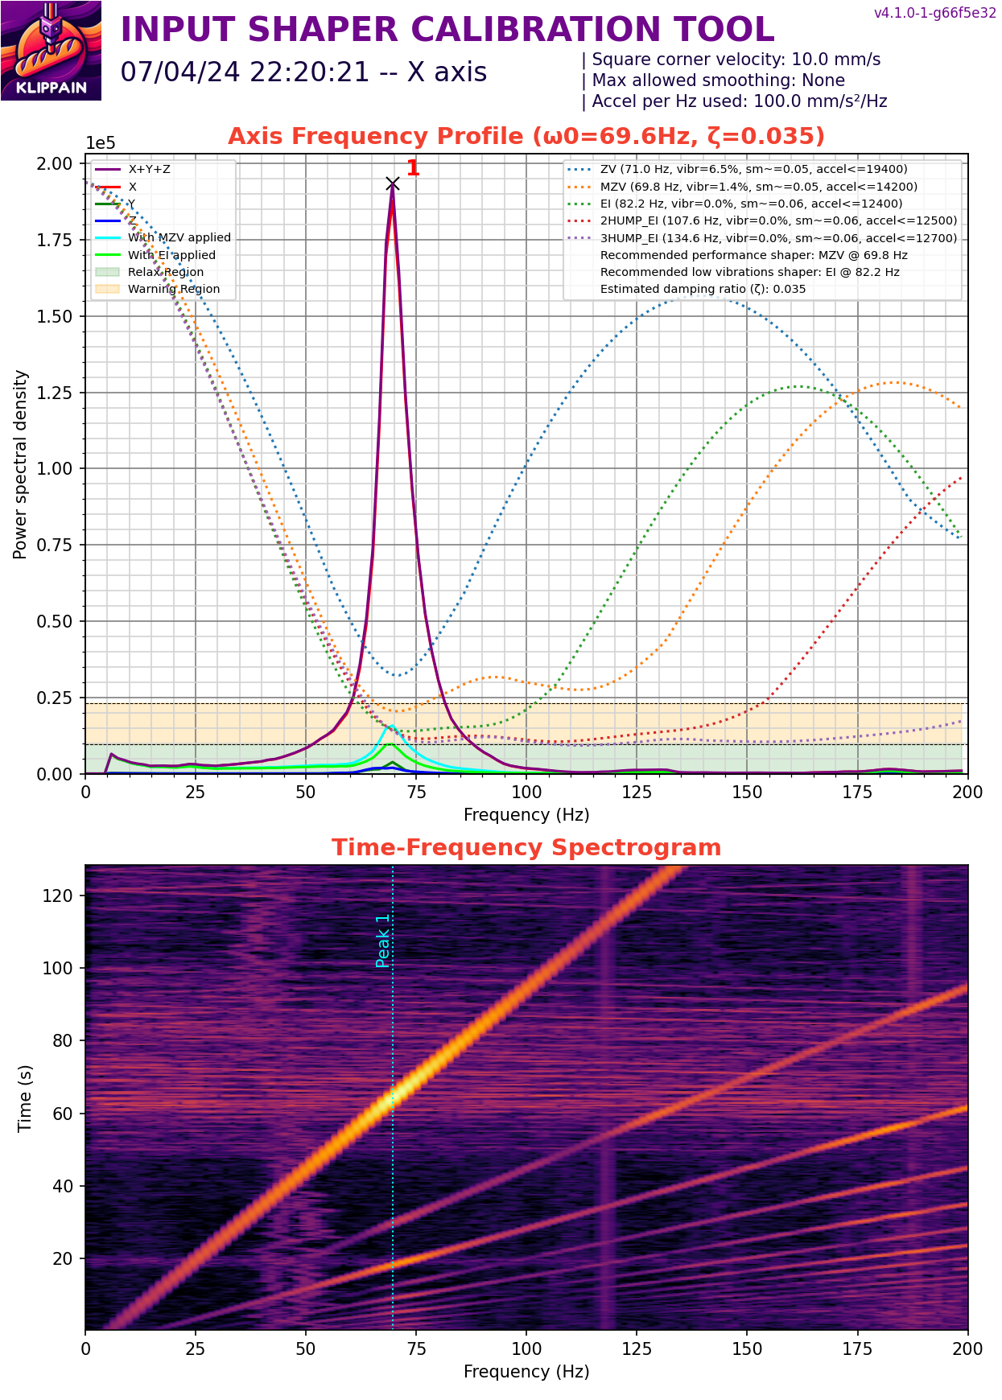
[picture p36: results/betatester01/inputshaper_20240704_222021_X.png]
bt01-metal-x
X |  | 
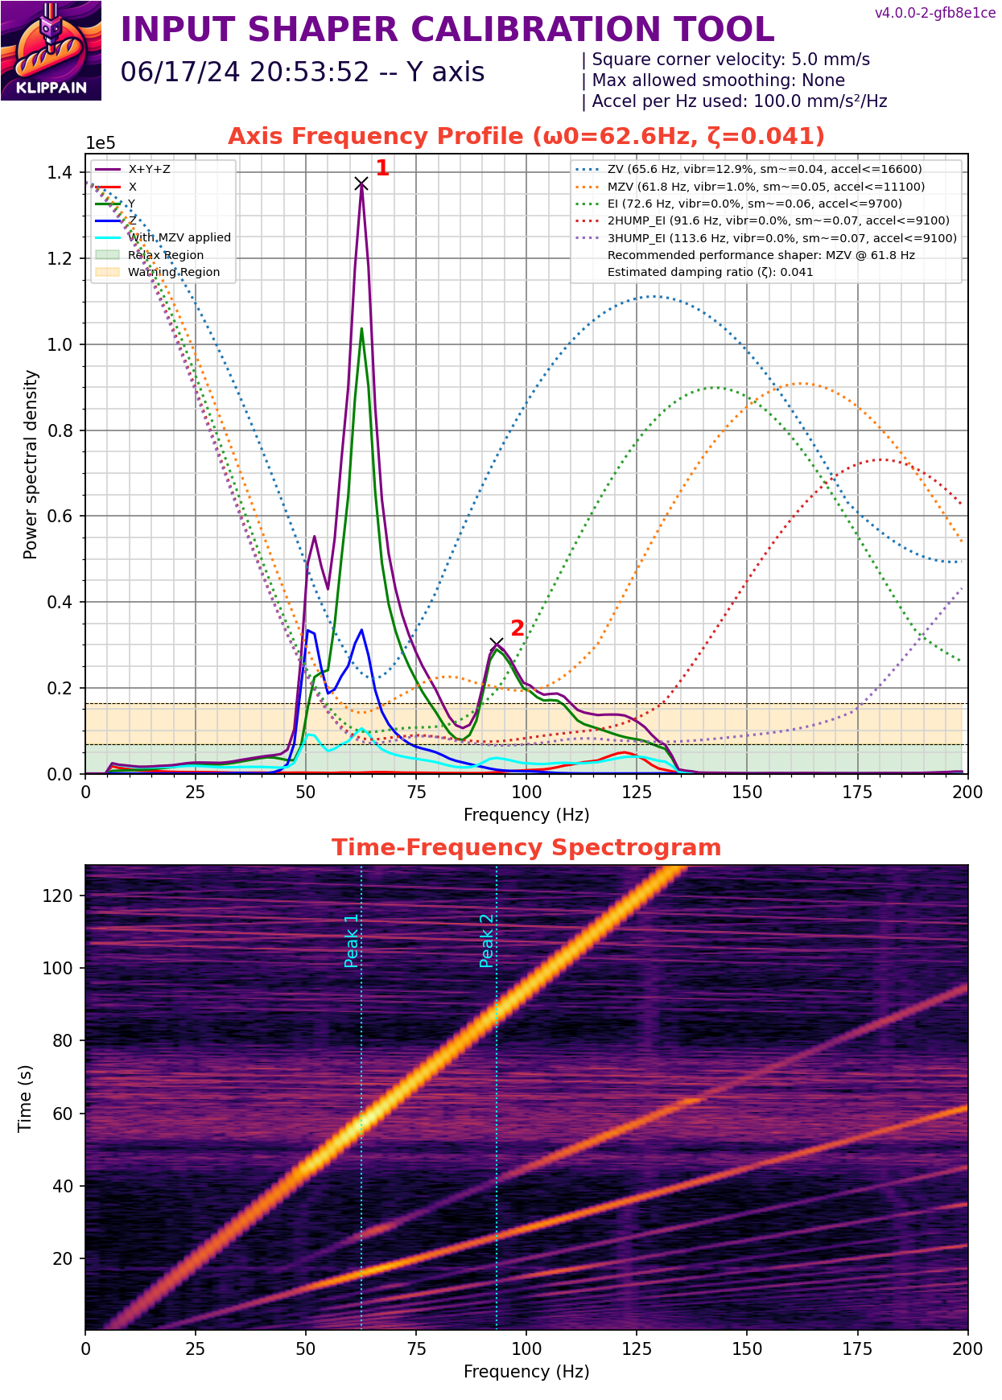
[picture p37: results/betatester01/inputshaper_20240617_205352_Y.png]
bt01-plastic-y
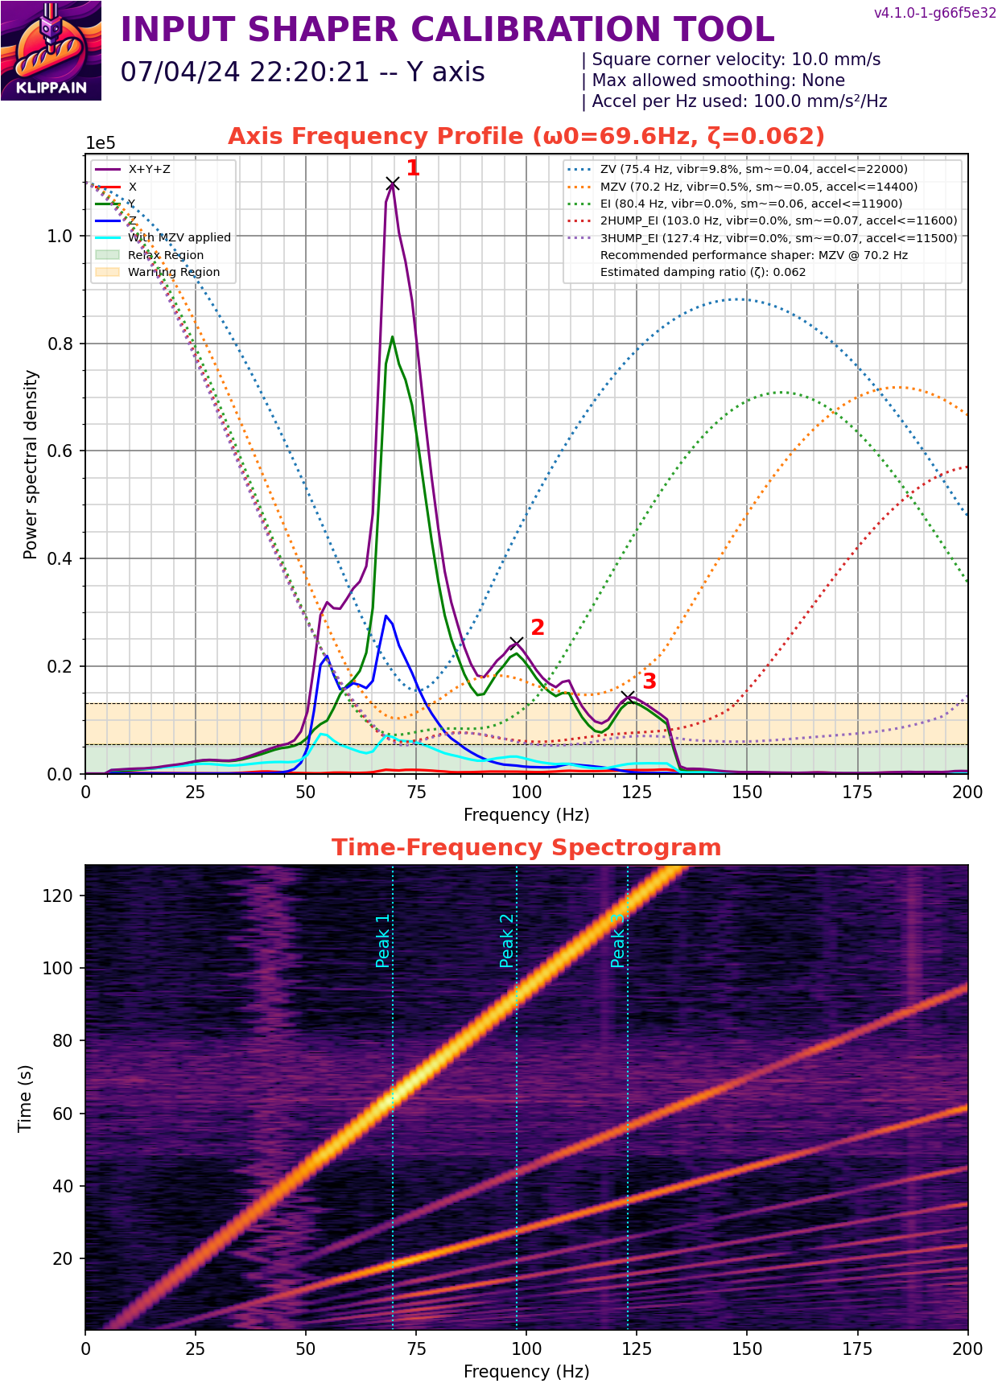
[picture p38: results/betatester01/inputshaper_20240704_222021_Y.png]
bt01-metal-y
Y |  |

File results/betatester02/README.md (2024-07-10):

Axis | Without Boop | Metal Boop
-----|--------------|-----------
X | bt02-noboop-x | bt02-metal-x
Y | bt02-noboop-y | bt02-metal-y

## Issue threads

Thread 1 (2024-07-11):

Dragon hotend fit issue

djeZo888, 2024-07-11:
Version affected: **Beta RC1** 2-part/3-part
Toolhead: **Dragon Burner v8**
Hotend: **Dragon SF/HF**

If using Dragon hotend with Dragon Burner v8 toolhead, about 1.5mm of silicone sock needs to be cut off for everything to fit. Otherwise there is conflict with MGW7C cart as visible in the picture.

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

djeZo888, 2024-09-06:
This issue is resolved in latest beta RC2.

Closed 2024-09-06.

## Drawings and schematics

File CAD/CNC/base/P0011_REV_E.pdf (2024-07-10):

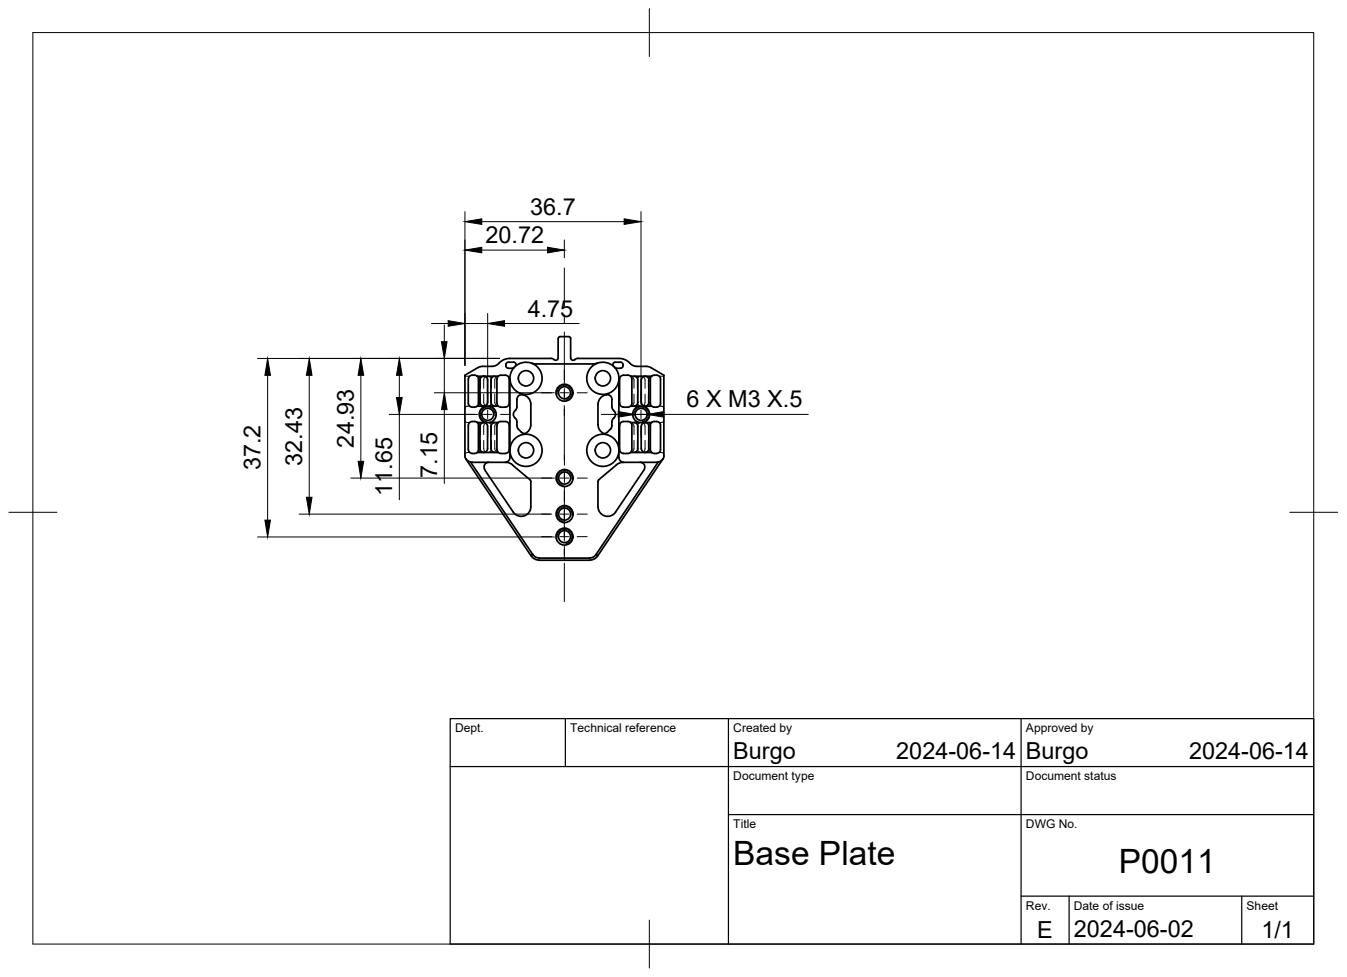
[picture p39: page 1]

Dept. | Technical reference | Created by Burgo 2024-06-14 | Approved by Burgo 2024-06-14

Document type | Document status

Title Base Plate | DWG No. P0011

Rev. E | Date of issue 2024-06-02 | Sheet 1/1

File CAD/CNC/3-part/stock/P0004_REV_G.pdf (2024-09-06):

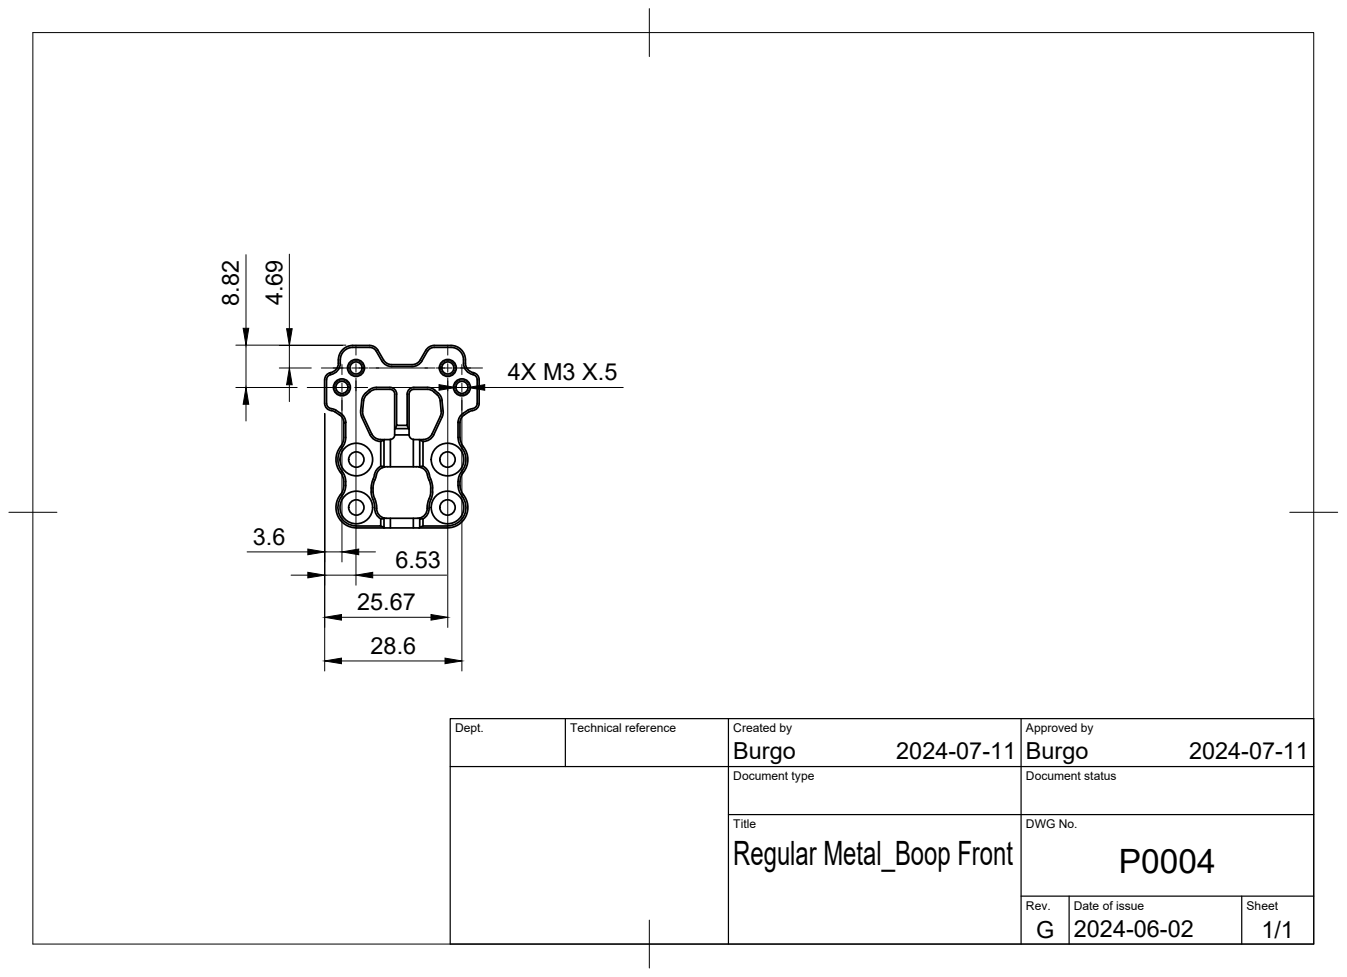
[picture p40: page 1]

Dept. | Technical reference | Created by Burgo 2024-07-11 | Approved by Burgo 2024-07-11

Document type | Document status

Title Regular Metal_Boop Front | DWG No. P0004

Rev. G | Date of issue 2024-06-02 | Sheet 1/1

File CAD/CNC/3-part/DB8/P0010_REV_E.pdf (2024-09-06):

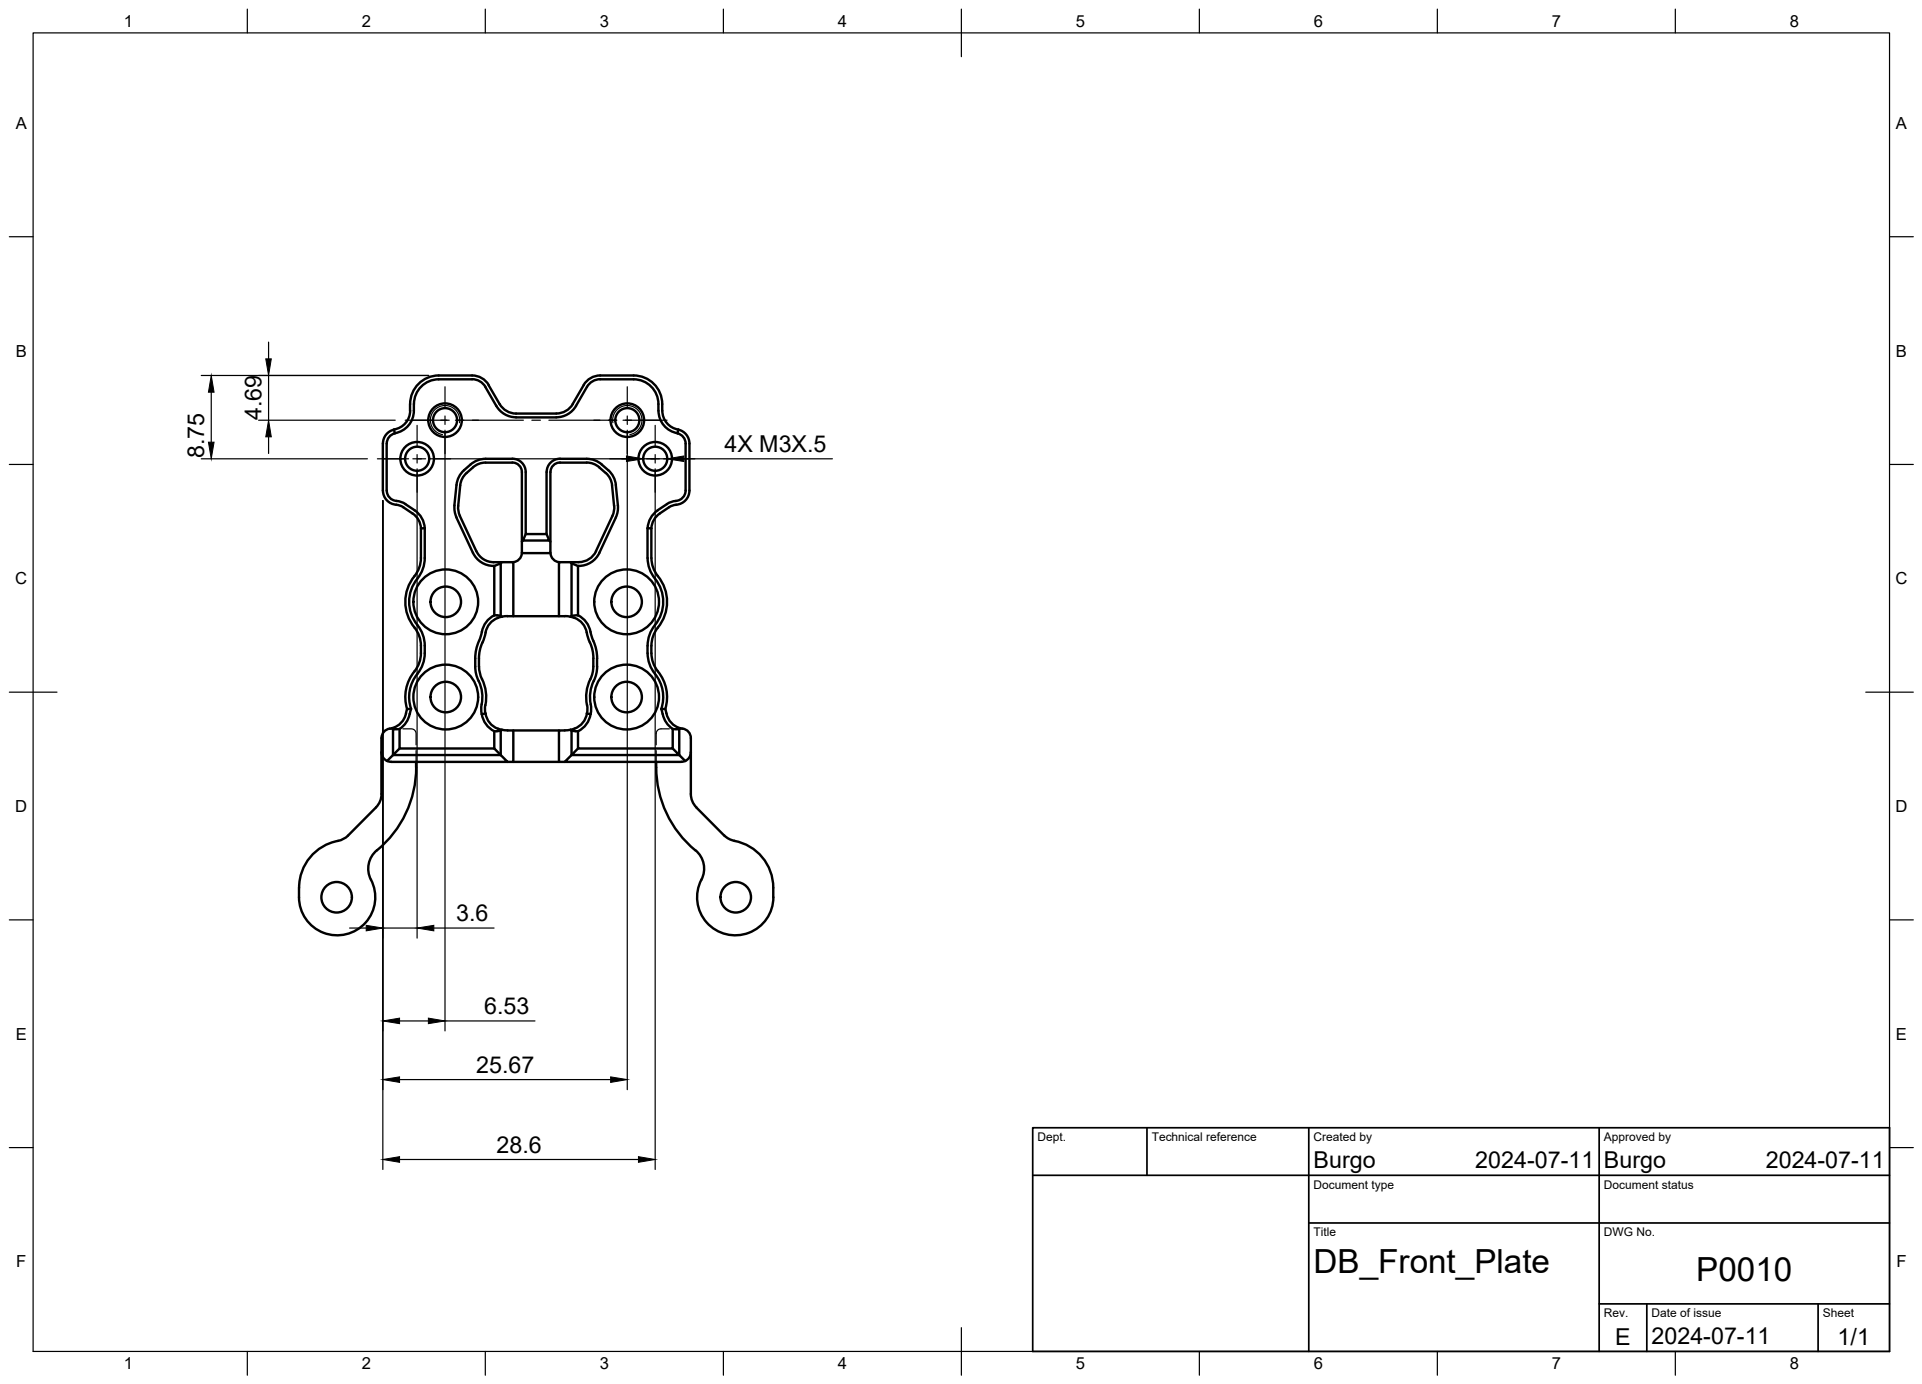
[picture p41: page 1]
Title; DWG No.; Rev.; Date of issue; Sheet

Dept. | Technical reference | Created by Burgo 2024-07-11 | Approved by Burgo 2024-07-11

Document type | Document status

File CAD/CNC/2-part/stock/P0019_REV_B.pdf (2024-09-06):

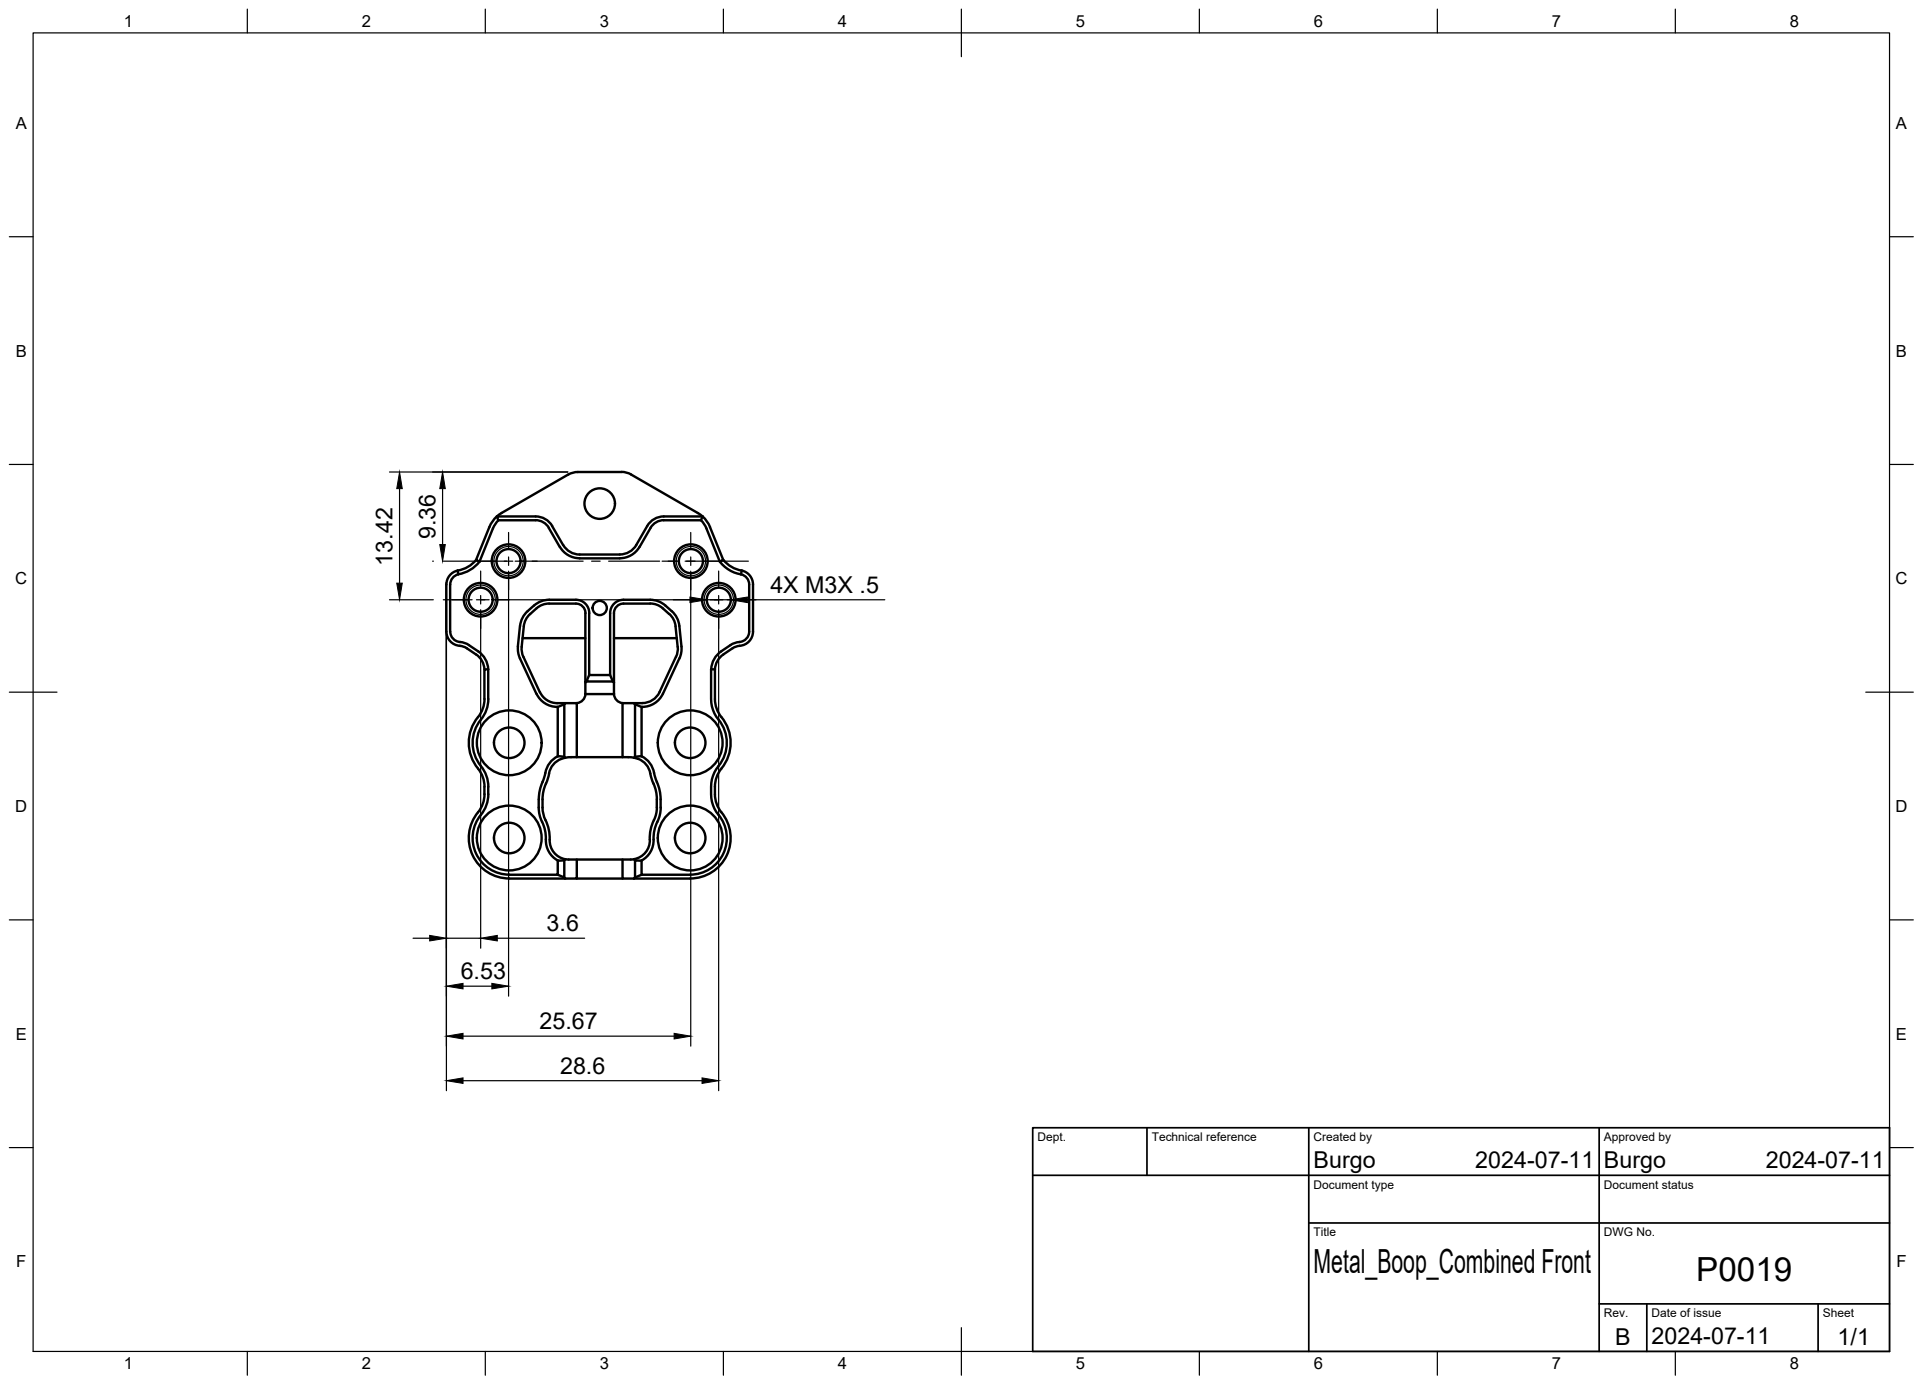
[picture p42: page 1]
Title; DWG No.; Rev.; Date of issue; Sheet; Metal_Boop_Combined Front; Burgo; Burgo 9.36 13.42

Dept. | Technical reference | Created by 2024-07-11 | Approved by 2024-07-11

Document type | Document status

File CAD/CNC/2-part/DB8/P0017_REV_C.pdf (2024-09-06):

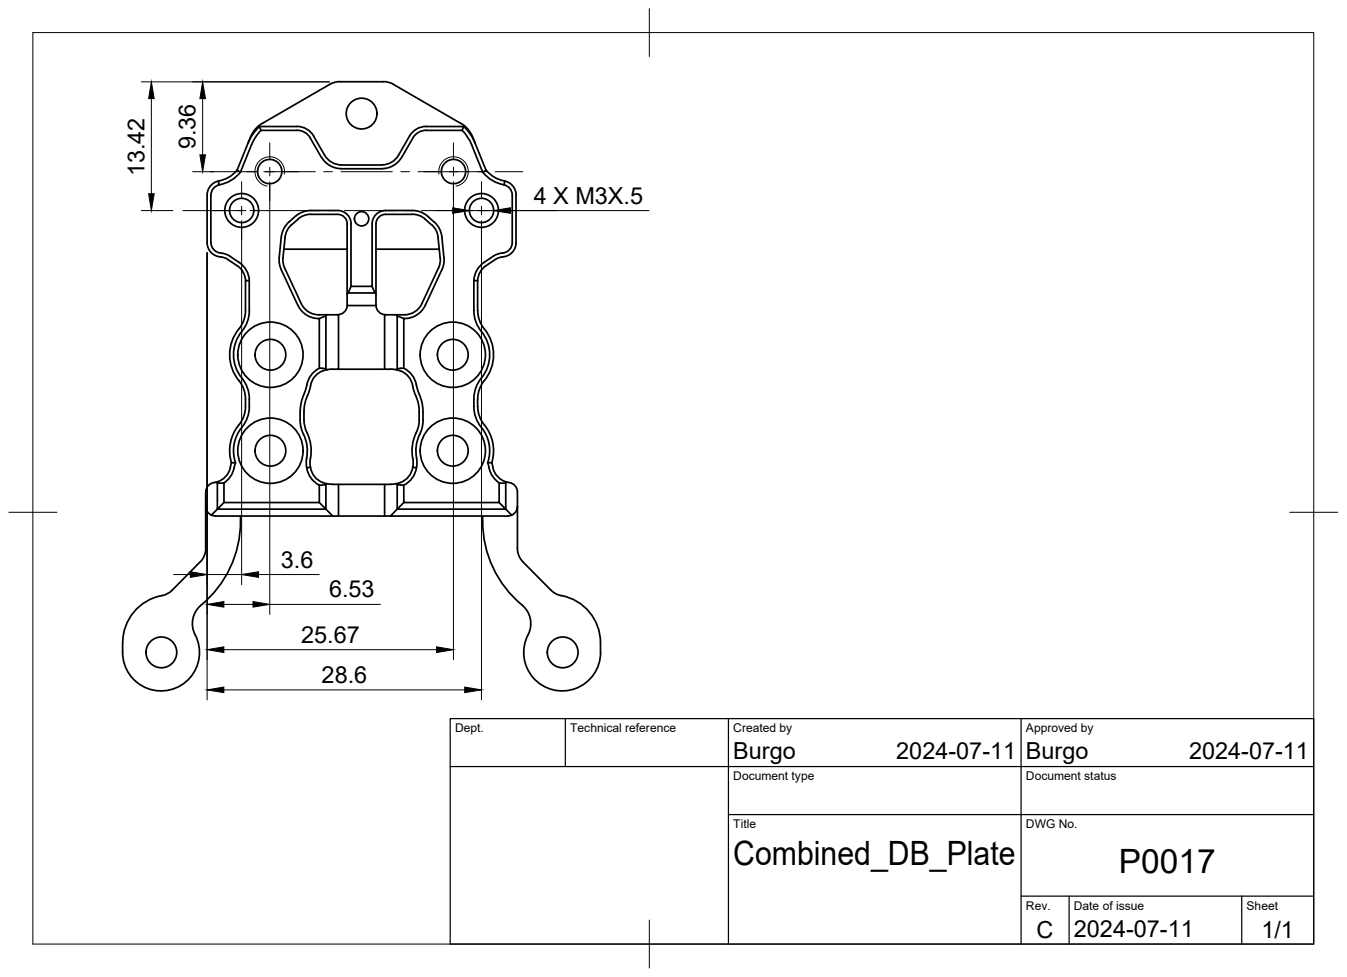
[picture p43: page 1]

Dept. | Technical reference | Created by Burgo 2024-07-11 | Approved by Burgo 2024-07-11

Document type | Document status

Title Combined_DB_Plate | DWG No. P0017

Rev. C | Date of issue 2024-07-11 | Sheet 1/1

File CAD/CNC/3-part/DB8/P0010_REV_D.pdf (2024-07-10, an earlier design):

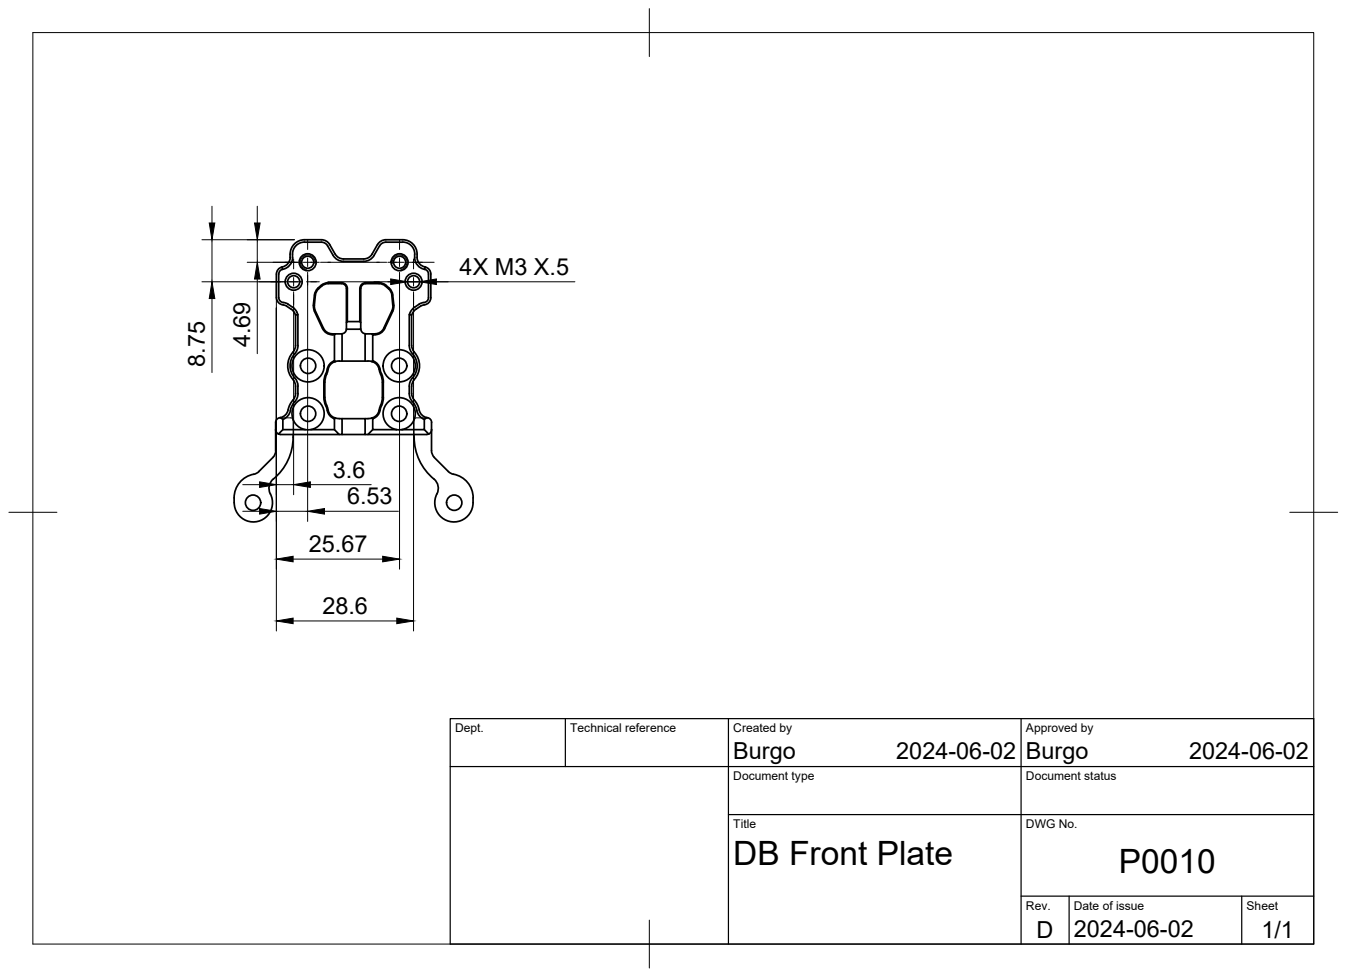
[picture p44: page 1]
Burgo; Burgo 8.75

Dept. | Technical reference | Created by 2024-06-02 | Approved by 2024-06-02

Document type | Document status

Title DB Front Plate | DWG No. P0010

Rev. D | Date of issue 2024-06-02 | Sheet 1/1

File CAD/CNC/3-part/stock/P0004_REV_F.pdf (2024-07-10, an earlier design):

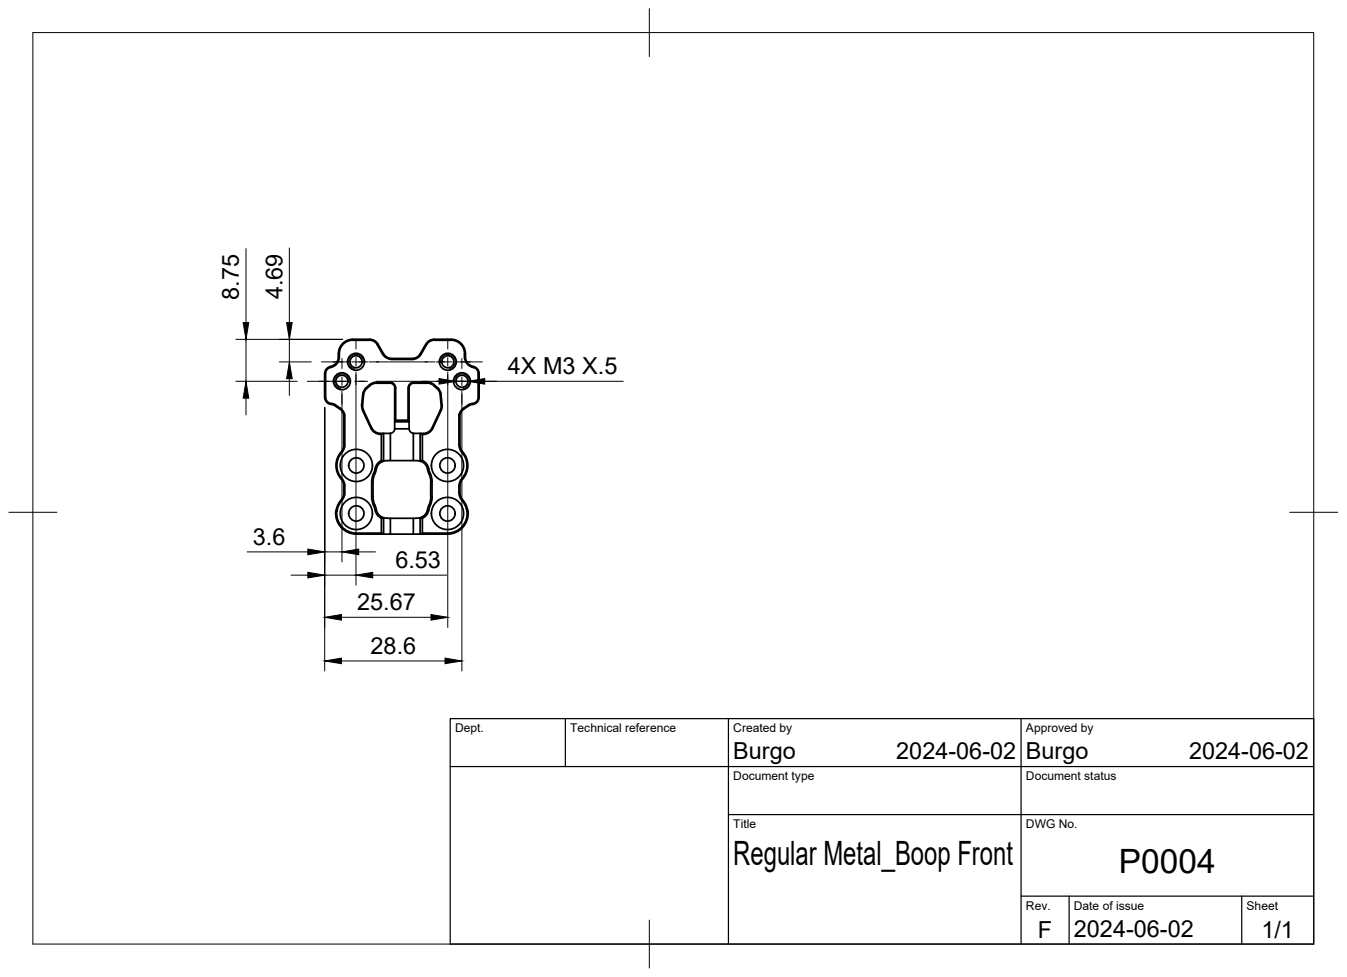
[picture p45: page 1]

Dept. | Technical reference | Created by Burgo 2024-06-02 | Approved by Burgo 2024-06-02

Document type | Document status

Title Regular Metal_Boop Front | DWG No. P0004

Rev. F | Date of issue 2024-06-02 | Sheet 1/1

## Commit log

2024-07-20 added BOM Linear rail link - Replimat
2024-09-06 added beta RC2 files
    [P0017_REV_C.step]
2024-09-06 updated to beta RC2 CAD file
2024-09-06 Update and rename P0010_REV_E .step to P0010_REV_E.step
    [P0010_REV_E.step]
2024-09-06 Updated links to PCBWAY Beta RC2
